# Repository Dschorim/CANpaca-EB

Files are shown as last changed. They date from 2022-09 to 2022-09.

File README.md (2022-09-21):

# CANpaca-EB
This is the extruder board from the CANpaca printer board family.

## Features
 - CAN input (with 7.5A@24V) input
 - 1 extrudder stepper (via tmc2130 with SPI control)
 - 2 PWM fans
 - support for klicky probe / bltouch
 - 1 hotend
 - 1 regular thermistor
 - 1 thermistor via MAX31865
 - ADXL345 Accererometer
 - runout sensor
 - RGB lighting

## Changelog

### V0.2
 - changed caps from 0603 to 0402
 - changed resistors from 0603 to 0402
 - decoupling caps are now properly placed close to power pins
 - added thermal vias below rp2040
 - increased via diameter from 0.4mm to 0.45mm to save cost
 - changed to hardware SPI pins

### V0.1
 - initial release

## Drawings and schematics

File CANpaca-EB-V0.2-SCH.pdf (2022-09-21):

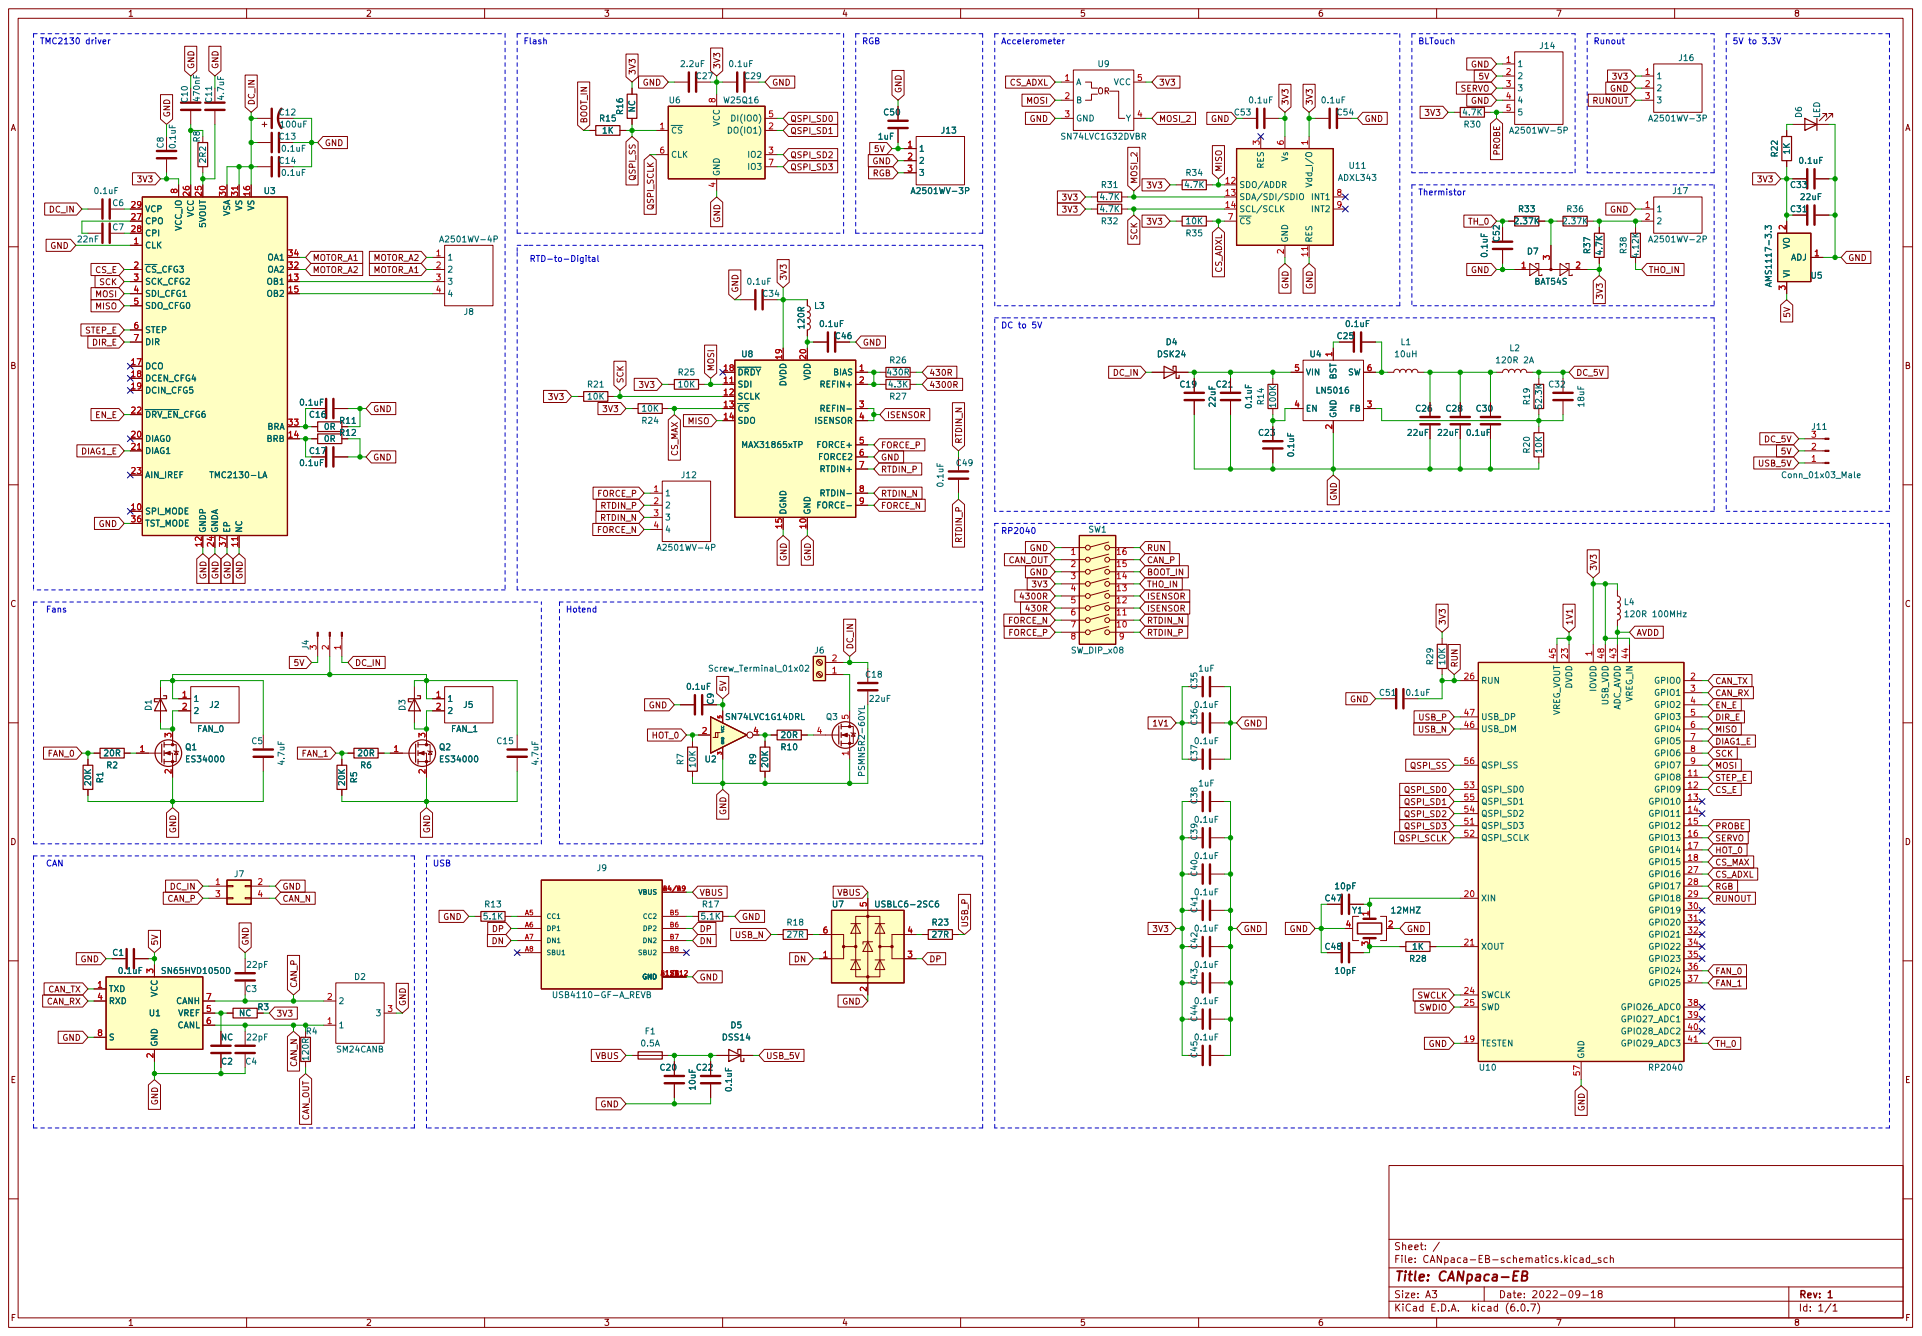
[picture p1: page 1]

1 RES 11 SDO/ADDR 12 SDA/SDI/SDIO 13 SCL/SCLK 14 GND

1 CLK 1 SPI_MODE 10 NC 11 GNDP 12 OB1 13 BRB 14 OB2 15 VS 16 DCO 17 DCEN_CFG4 18 DCIN_CFG5 19 ~{CS}_CFG3 2 DIAG0 20 DIAG1 21 ~{DRV_EN}_CFG6 22 AIN_IREF 23 GNDA 24 5VOUT 25 VCC 26 CPO 27 CPI 28 VCP 29 SCK_CFG2 3 VSA 30 VS 31 OA2 32 BRA 33 OA1 34 TST_MODE 36 EP 37 SDI_CFG1 4 SDO_CFG0 5 STEP 6 DIR 7 VCC_IO

2 FB 3 EN 4 VIN 5 SW 6 C19 22uF D4 DSK24 C25
22uF D4 DSK24

2 FB 3 EN 4 VIN 5 SW 6 U4
LN5016 BST

3 RXD 4 VREF 5 CANL 6 CANH 7 S

File: CANpaca-EB-schematics.kicad_sch Sheet: /
Id: 1/1 Title: CANpaca-EB

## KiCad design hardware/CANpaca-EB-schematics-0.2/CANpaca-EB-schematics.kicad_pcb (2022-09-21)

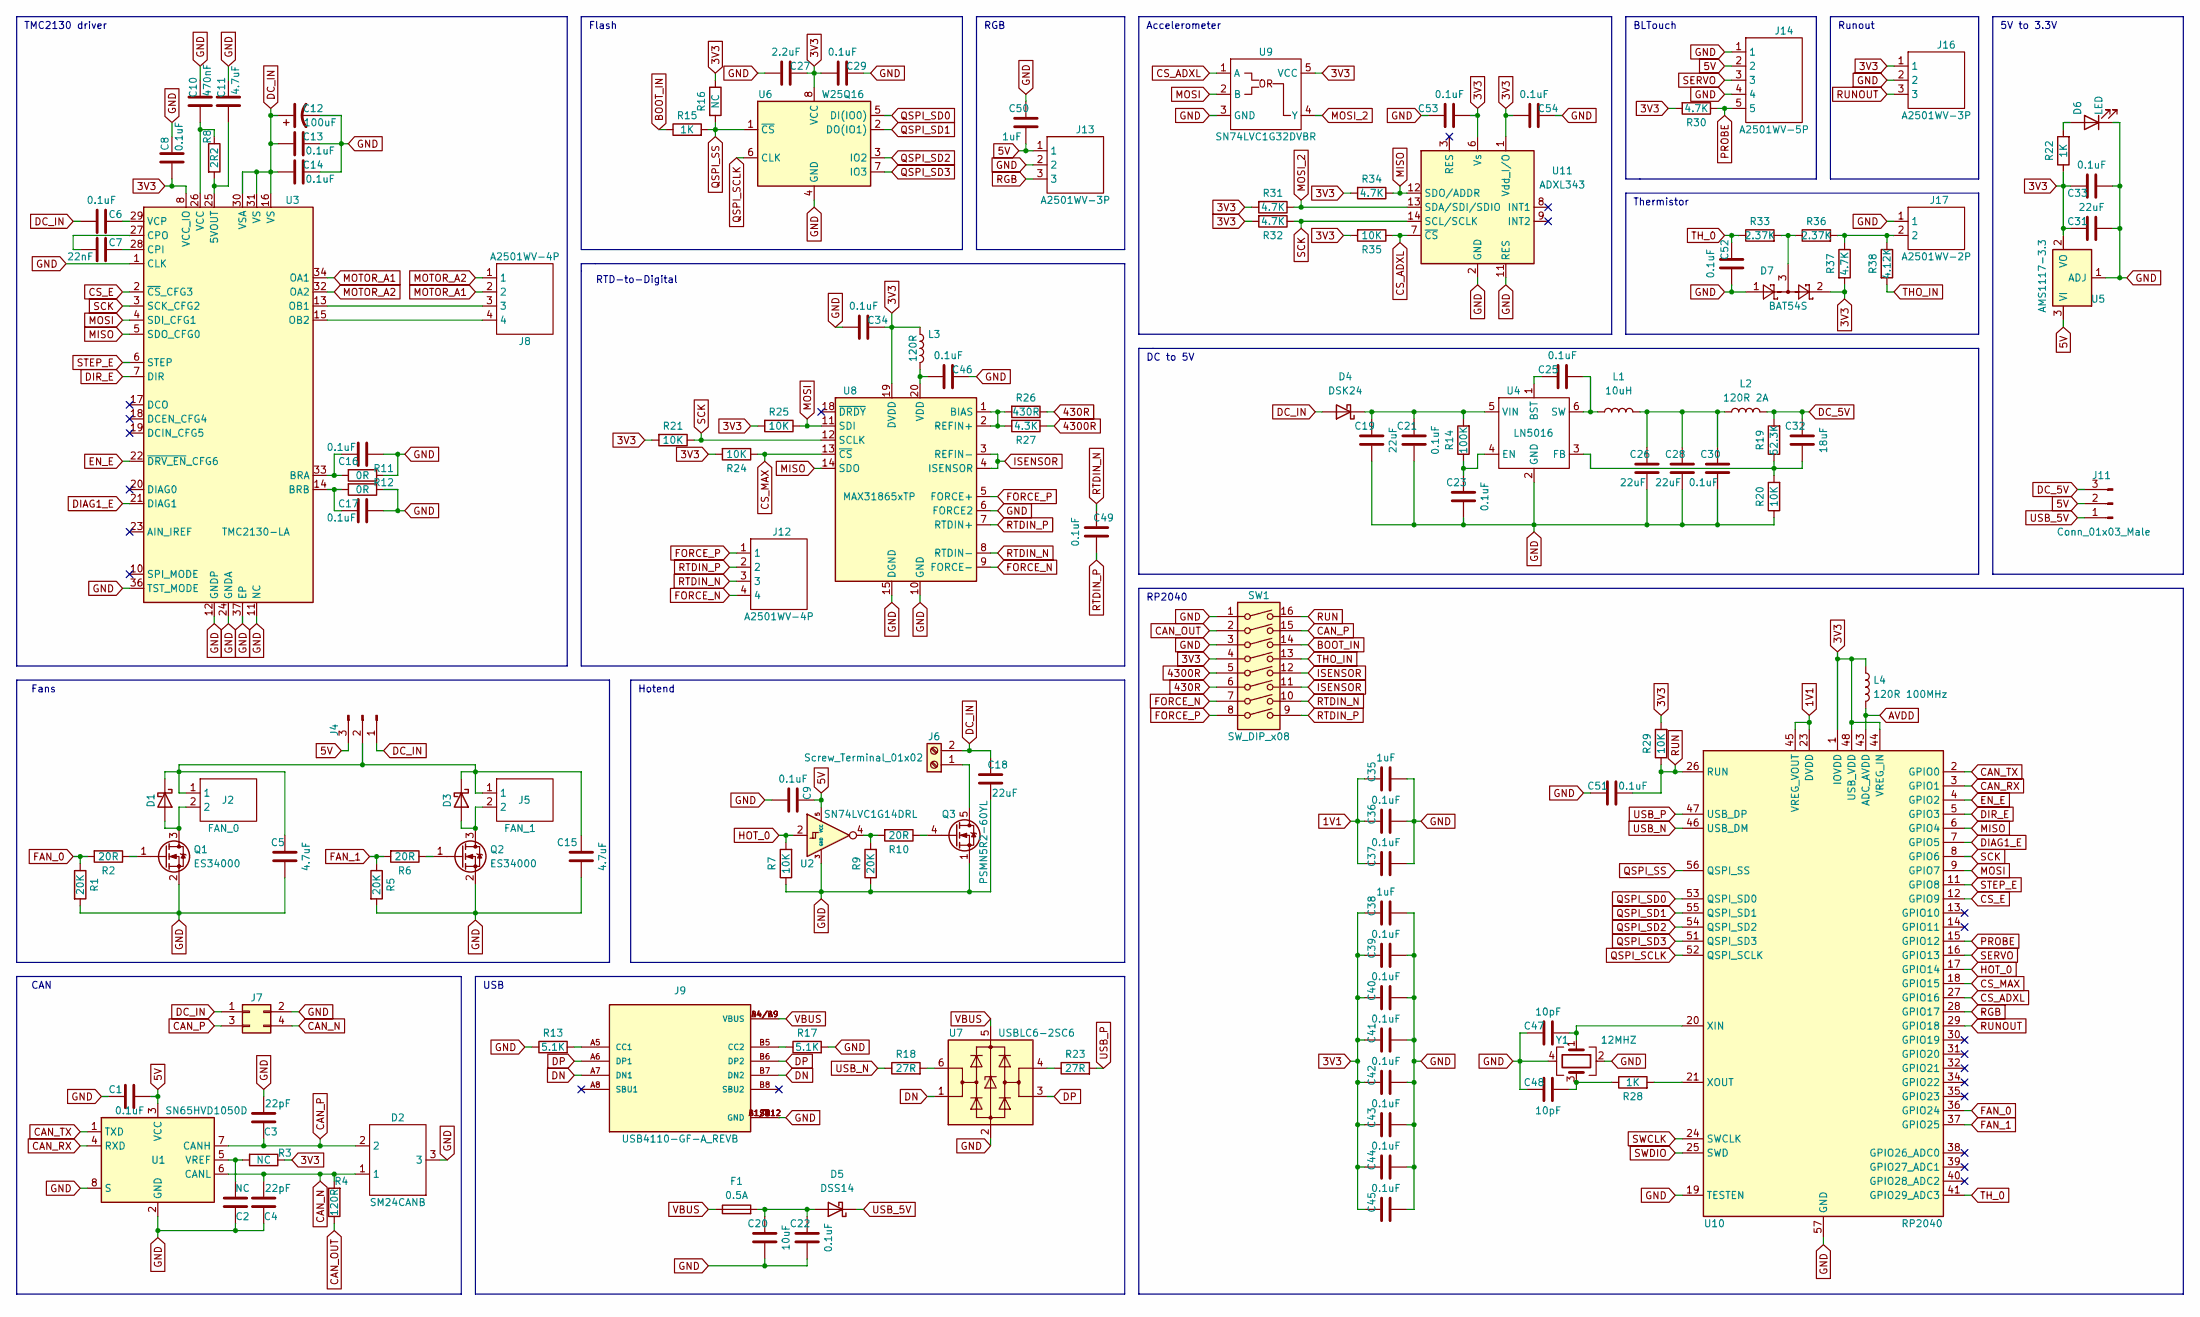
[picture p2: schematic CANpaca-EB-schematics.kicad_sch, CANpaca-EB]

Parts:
C1, C6, C8, C9, C13, C14, C16, C17, C21, C22, C23, C25, C29, C30, C33, C34, C36, C37, C39, C40, C41, C42, C43, C44, C45, C46, C49, C51, C52, C53, C54: 0.1uF; C_0402_1005Metric
C2: NC; C_0402_1005Metric
C3, C4: 22pF; C_0402_1005Metric
C5, C11, C15: 4.7uF; C_0402_1005Metric
C7: 22nF; C_0402_1005Metric
C10: 470nF; C_0402_1005Metric
C12: 100uF; CP_Elec_10x14.3
C18, C19, C26, C28, C31: 22uF; C_0402_1005Metric
C20: 10uF; C_0402_1005Metric
C27: 2.2uF; C_0402_1005Metric
C32: 18uF; C_0402_1005Metric
C35, C38, C50: 1uF; C_0402_1005Metric
C47, C48: 10pF; C_0402_1005Metric
D1, D3: D_Schottky; D_SOD-323
D2: SM24CANB; SOT-23
D4: DSK24; D_SOD-123
D5: DSS14; D_SOD-123F
D6: LED; LED_0603_1608Metric
D7: BAT54S; SOT-23
F1: 0.5A; Fuse_BelFuse_0ZRE0005FF_L8.3mm_W3.8mm
J2: FAN_0; A2501WV-2P
J4, J11: Conn_01x03_Male; PinHeader_1x03_P2.54mm_Vertical
J5: FAN_1; A2501WV-2P
J6: Screw_Terminal_01x02; KF350-2P
J7: Conn_02x02_Odd_Even; Molex_Micro-Fit_3.0_43045-0400_2x02_P3.00mm_Horizontal
J8: A2501WV-4P
J9: USB4110-GF-A_REVB; GCT_USB4110-GF-A_REVB; PARTREV B
J12: A2501WV-4P; A1250WV-4P
J13, J16: A2501WV-3P; A1250WV-3P
J14: A2501WV-5P; A1250WV-5P
J17: A2501WV-2P
L1: 10uH; L_0603_1608Metric
L2: 120R 2A; L_0805_2012Metric
L3: 120R; L_0805_2012Metric
L4: 120R 100MHz; L_0603_1608Metric
Q1, Q2: ES34000; SOT-23
Q3: PSMN5R2-60YL; LFPAK56
R1, R5, R9: 20K; R_0402_1005Metric
R2, R6, R10: 20R; R_0402_1005Metric
R3, R16: NC; R_0402_1005Metric
R4: 120R; R_0402_1005Metric
R7, R20, R21, R24, R25, R29, R35: 10K; R_0402_1005Metric
R8: 2R2; R_0402_1005Metric
R11, R12: 0R; R_0402_1005Metric
R13, R17: 5.1K; R_0402_1005Metric
R14: 100K; R_0402_1005Metric
R15, R22, R28: 1K; R_0402_1005Metric
R18, R23: 27R; R_0402_1005Metric
R19: 52.3K; R_0402_1005Metric
R26: 430R; R_0402_1005Metric
R27: 4.3K; R_0402_1005Metric
R30, R31, R32, R34, R37: 4.7K; R_0402_1005Metric
R33, R36: 2.37K; R_0402_1005Metric
R38: 4.12K; R_0402_1005Metric
SW1: SW_DIP_x08; SW_DIP_SPSTx08_Slide_Copal_CHS-08B_W7.62mm_P1.27mm
U1: SN65HVD1050D; SOIC-8_3.9x4.9mm_P1.27mm
U2: SN74LVC1G14DRL; SOT-553
U3: TMC2130-LA; QFN-36-1EP_5x6mm_P0.5mm_EP3.6x4.1mm
U4: LN5016; SOT-23-6
U5: AMS1117-3.3; SOT-223-3_TabPin2
U6: W25Q16; SOIC-8_3.9x4.9mm_P1.27mm
U7: USBLC6-2SC6; SOT-23-6
U8: MAX31865xTP; TQFN-20-1EP_5x5mm_P0.65mm_EP3.25x3.25mm
U9: SN74LVC1G32DVBR; SOT-23-5
U10: RP2040; QFN-56-1EP_7x7mm_P0.4mm_EP3.2x3.2mm
U11: ADXL343; LGA-14_3x5mm_P0.8mm_LayoutBorder1x6y
Y1: 12MHZ; Crystal_SMD_3225-4Pin_3.2x2.5mm

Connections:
1V1: C35.2, C36.2, C37.2, U10.23 (DVDD), U10.45 (VREG_VOUT), U10.50 (DVDD)
3V3: C8.2, C27.1, C29.2, C31.2, C33.2, C34.1, C38.2, C39.2, C40.2, C41.2, C42.2, C43.2, C44.2, C45.2, C53.1, C54.2, D7.2, J16.1, L3.1, L4.1, R3.1, R16.1, R21.2, R22.1, R24.2, R25.2, R29.2, R30.2, R31.2, R32.2, R34.2, R35.2, R37.2, SW1.4, U3.8 (VCC_IO), U5.2 (VO), U6.8 (VCC), U8.19 (DVDD), U9.5 (VCC), U10.1 (IOVDD), U10.10 (IOVDD), U10.22 (IOVDD), U10.33 (IOVDD), U10.42 (IOVDD), U10.44 (VREG_IN), U10.48 (USB_VDD), U10.49 (IOVDD), U11.1 (Vdd_I/O), U11.6 (Vs)
5V: C1.2, C9.2, C50.1, J4.3, J11.2, J13.1, J14.2, U1.3 (VCC), U2.5 (VCC), U5.3 (VI)
430R: R26.1, SW1.6
4300R: R27.1, SW1.5
AVDD: L4.2, U10.43 (ADC_AVDD)
BOOT_IN: R15.1, SW1.14
CAN_N: C4.2, D2.1, J7.4, R4.2, U1.6 (CANL)
CAN_OUT: R4.1, SW1.2
CAN_P: C3.1, D2.2, J7.3, SW1.15, U1.7 (CANH)
CAN_RX: U1.4 (RXD), U10.3 (GPIO1)
CAN_TX: U1.1 (TXD), U10.2 (GPIO0)
CS_ADXL: R35.1, U9.1 (A), U10.27 (GPIO16), U11.7 (~CS)
CS_E: U3.2 (~CS_CFG3), U10.12 (GPIO9)
CS_MAX: R24.1, U8.13 (~CS), U10.18 (GPIO15)
DC_5V: C32.2, J11.3, L2.2, R19.2
DC_IN: C6.1, C12.1, C13.2, C14.2, C18.2, D4.2 (A), J4.1, J6.2, J7.1, U3.16 (VS), U3.30 (VSA), U3.31 (VS)
DIAG1_E: U3.21 (DIAG1), U10.7 (GPIO5)
DIR_E: U3.7 (DIR), U10.5 (GPIO3)
DN: J9.A7 (DN1), J9.B7 (DN2), U7.1 (I/O1)
DP: J9.A6 (DP1), J9.B6 (DP2), U7.3 (I/O2)
EN_E: U3.22 (~DRV_EN_CFG6), U10.4 (GPIO2)
FAN_0: R1.1, R2.2, U10.36 (GPIO24)
FAN_1: R5.1, R6.2, U10.37 (GPIO25)
FORCE_N: J12.4, SW1.7, U8.9 (FORCE-)
FORCE_P: J12.1, SW1.8, U8.5 (FORCE+)
GND: C1.1, C2.1, C3.2, C4.1, C5.1, C8.1, C9.1, C10.1, C11.1, C12.2, C13.1, C14.1, C15.1, C16.2, C17.2, C18.1, C19.1, C20.1, C21.1, C22.1, C23.1, C26.1, C27.2, C28.1, C29.1, C30.1, C31.1, C33.1, C34.2, C35.1, C36.1, C37.1, C38.1, C39.1, C40.1, C41.1, C42.1, C43.1, C44.1, C45.1, C46.1, C47.1, C48.1, C50.2, C51.1, C52.2, C53.2, C54.1, D2.3, D6.1 (K), D7.1, J7.2, J9.A1/B12 (GND), J9.B1/A12 (GND), J9.S1 (GND), J9.S2 (GND), J9.S3 (GND), J9.S4 (GND), J13.2, J14.1, J14.4, J16.2, J17.1, Q1.2 (S), Q2.2 (S), Q3.1 (S), Q3.2 (S), Q3.3 (S), R1.2, R5.2, R7.1, R9.1, R11.1, R12.1, R13.1, R17.2, R20.1, SW1.1, SW1.3, U1.2 (GND), U1.8 (S), U2.3 (GND), U3.1 (CLK), U3.11 (NC), U3.12 (GNDP), U3.24 (GNDA), U3.35 (GNDP), U3.36 (TST_MODE), U3.37 (EP), U4.2 (GND), U5.1 (ADJ), U6.4 (GND), U7.2 (GND), U8.6 (FORCE2), U8.10 (GND), U8.15 (DGND), U8.16 (GND), U8.21 (GND), U9.3 (GND), U10.19 (TESTEN), U10.57 (GND), U11.2 (GND), U11.4 (GND), U11.5 (GND), U11.11 (RES), Y1.2, Y1.4
HOT_0: R7.2, U2.2, U10.17 (GPIO14)
ISENSOR: SW1.11, SW1.12, U8.3 (REFIN-), U8.4 (ISENSOR)
MISO: R34.1, U3.5 (SDO_CFG0), U8.14 (SDO), U10.6 (GPIO4), U11.12 (SDO/ADDR)
MOSI: R25.1, U3.4 (SDI_CFG1), U8.11 (SDI), U9.2 (B), U10.9 (GPIO7)
MOSI_2: R31.1, U9.4 (Y), U11.13 (SDA/SDI/SDIO)
MOTOR_A1: J8.2, U3.34 (OA1)
MOTOR_A2: J8.1, U3.32 (OA2)
unnamed: C2.2, R3.2, U1.5 (VREF)
unnamed: C6.2, U3.29 (VCP)
unnamed: C7.1, U3.27 (CPO)
unnamed: C7.2, U3.28 (CPI)
unnamed: C10.2, R8.1, U3.26 (VCC)
unnamed: C11.2, R8.2, U3.25 (5VOUT)
unnamed: C5.2, C15.2, D1.1 (K), D3.1 (K), J2.1, J4.2, J5.1
unnamed: C16.1, R11.2, U3.33 (BRA)
unnamed: C17.1, R12.2, U3.14 (BRB)
unnamed: C19.2, C21.2, D4.1 (K), R14.2, U4.5 (VIN)
unnamed: C20.2, C22.2, D5.2 (A), F1.2
unnamed: C23.2, R14.1, U4.4 (EN)
unnamed: C25.1, L1.1, U4.6 (SW)
unnamed: C25.2, U4.1 (BST)
unnamed: C26.2, C28.2, C30.2, L1.2, L2.1
unnamed: C32.1, R19.1, R20.2, U4.3 (FB)
unnamed: C46.2, L3.2, U8.20 (VDD)
unnamed: C47.2, U10.20 (XIN), Y1.1
unnamed: C48.2, R28.1, Y1.3
unnamed: D1.2 (A), J2.2, Q1.3 (D)
unnamed: D3.2 (A), J5.2, Q2.3 (D)
unnamed: D6.2 (A), R22.2
unnamed: D7.3, R33.2, R36.1
unnamed: J6.1, Q3.5 (D)
unnamed: J8.3, U3.13 (OB1)
unnamed: J8.4, U3.15 (OB2)
unnamed: J9.A5 (CC1), R13.2
unnamed: J9.B5 (CC2), R17.1
unnamed: J17.2, R36.2, R37.1, R38.1
unnamed: Q1.1 (G), R2.1
unnamed: Q2.1 (G), R6.1
unnamed: Q3.4 (G), R10.1
unnamed: R9.2, R10.2, U2.4
unnamed: R18.2, U7.6 (I/O1)
unnamed: R23.1, U7.4 (I/O2)
unnamed: R26.2, R27.2, U8.1 (BIAS), U8.2 (REFIN+)
unnamed: R28.2, U10.21 (XOUT)
PROBE: J14.5, R30.1, U10.15 (GPIO12)
QSPI_SCLK: U6.6 (CLK), U10.52 (QSPI_SCLK)
QSPI_SD0: U6.5 (DI(IO0)), U10.53 (QSPI_SD0)
QSPI_SD1: U6.2 (DO(IO1)), U10.55 (QSPI_SD1)
QSPI_SD2: U6.3 (IO2), U10.54 (QSPI_SD2)
QSPI_SD3: U6.7 (IO3), U10.51 (QSPI_SD3)
QSPI_SS: R15.2, R16.2, U6.1 (~CS), U10.56 (QSPI_SS)
RGB: J13.3, U10.28 (GPIO17)
RTDIN_N: C49.2, J12.3, SW1.10, U8.8 (RTDIN-)
RTDIN_P: C49.1, J12.2, SW1.9, U8.7 (RTDIN+)
RUN: C51.2, R29.1, SW1.16, U10.26 (RUN)
RUNOUT: J16.3, U10.29 (GPIO18)
SCK: R21.1, R32.1, U3.3 (SCK_CFG2), U8.12 (SCLK), U10.8 (GPIO6), U11.14 (SCL/SCLK)
SERVO: J14.3, U10.16 (GPIO13)
STEP_E: U3.6 (STEP), U10.11 (GPIO8)
SWCLK: U10.24 (SWCLK)
SWDIO: U10.25 (SWD)
THO_IN: R38.2, SW1.13
TH_0: C52.1, R33.1, U10.41 (GPIO29_ADC3)
USB_5V: D5.1 (K), J11.1
USB_N: R18.1, U10.46 (USB_DM)
USB_P: R23.2, U10.47 (USB_DP)
VBUS: F1.1, J9.A4/B9 (VBUS), J9.B4/A9 (VBUS), U7.5 (VBUS)

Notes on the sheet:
5V to 3.3V
Fans
TMC2130 driver
Flash
USB
BLTouch
RP2040
Accelerometer
RGB
Runout
Hotend
RTD-to-Digital
Thermistor
CAN
DC to 5V

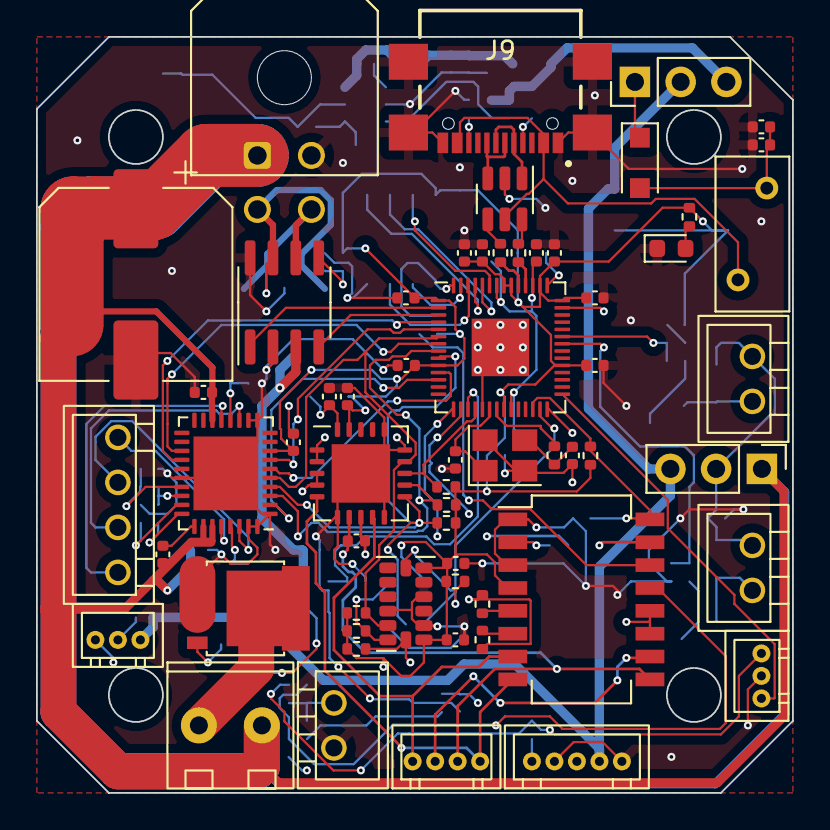
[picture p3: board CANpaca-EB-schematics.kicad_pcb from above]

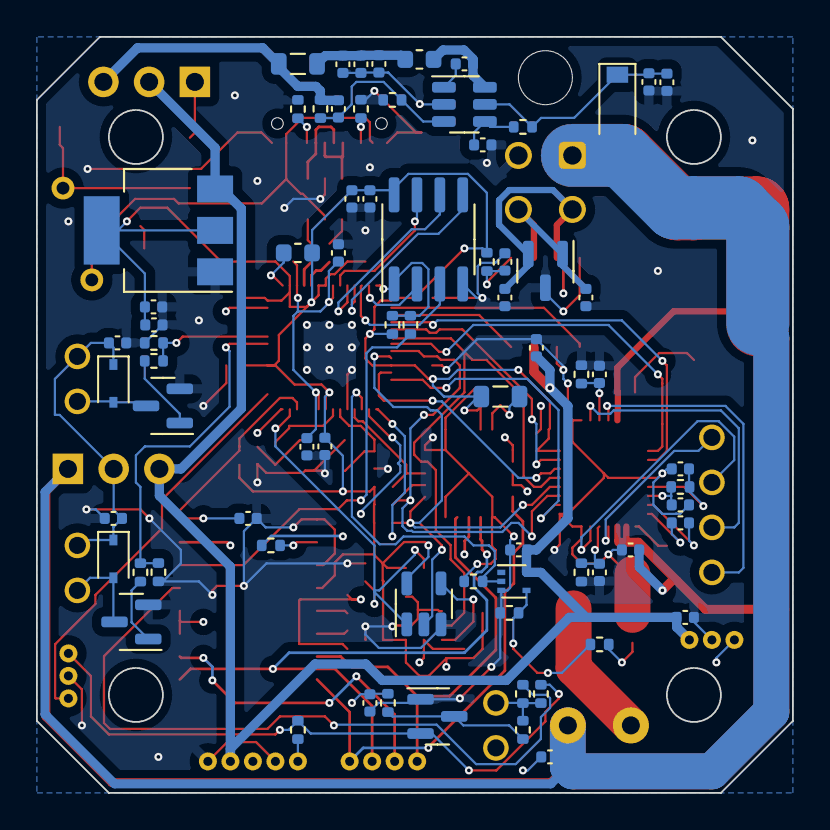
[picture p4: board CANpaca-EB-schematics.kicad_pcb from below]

Board: 4 copper layers, 42.0 x 42.0 mm, 132 parts (72 on the bottom side), 92 nets.

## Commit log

2022-09-14 added some schematics
    [CANpaca-EB-schematics.kicad_pcb, CANpaca-EB-schematics.kicad_sch]
2022-09-15 more stuff + todo added
    [CANpaca-EB-schematics.kicad_sch]
2022-09-18 finished schematics
    [CANpaca-EB-schematics.kicad_sch]
2022-09-20 finished pcb
    [CANpaca-EB-schematics-B_Cu.gbr, CANpaca-EB-schematics-B_Mask.gbr, CANpaca-EB-schematics-B_Paste.gbr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]
2022-09-20 added schematic pdf
    [CANpaca-EB-schematics.kicad_pcb, CANpaca-EB-schematics.kicad_sch]
2022-09-21 fixed usb resistor
    [CANpaca-EB-schematics-B_Cu.gbr, CANpaca-EB-schematics-B_Mask.gbr, CANpaca-EB-schematics-B_Paste.gbr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]
2022-09-21 updated to V0.2
    [CANpaca-EB-schematics-B_Cu.gbr, CANpaca-EB-schematics-B_Mask.gbr, CANpaca-EB-schematics-B_Paste.gbr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]
2022-09-21 increased via size
    [CANpaca-EB-schematics-B_Cu.gbr, CANpaca-EB-schematics-B_Mask.gbr, CANpaca-EB-schematics-B_Paste.gbr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]
2022-09-21 changed to hardware spi
    [CANpaca-EB-schematics-B_Cu.gbr, CANpaca-EB-schematics-B_Mask.gbr, CANpaca-EB-schematics-B_Paste.gbr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]
